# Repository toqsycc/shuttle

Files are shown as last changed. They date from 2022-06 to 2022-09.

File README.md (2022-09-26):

# Колёсный робот на базе Arduino
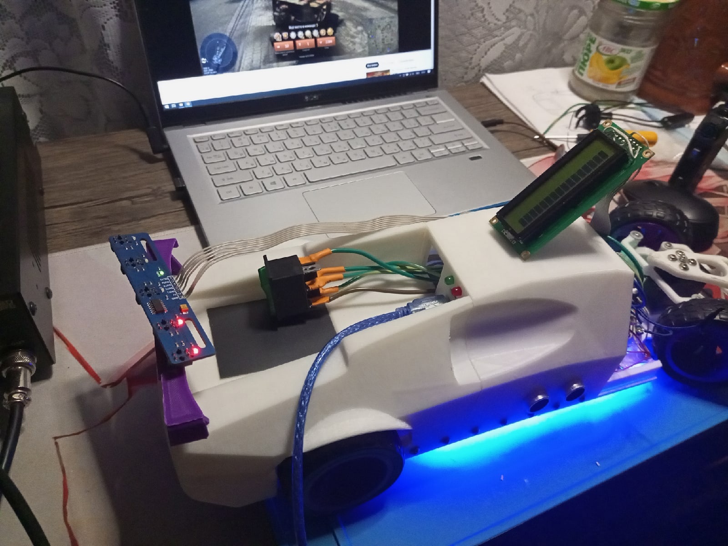
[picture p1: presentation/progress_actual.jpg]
Общий вид сборки

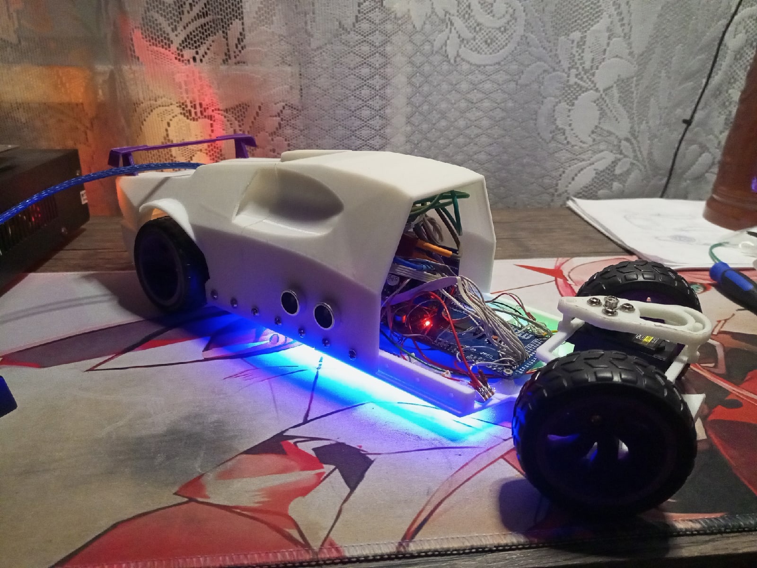
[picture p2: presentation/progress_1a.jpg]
Прогресс сборки, 1

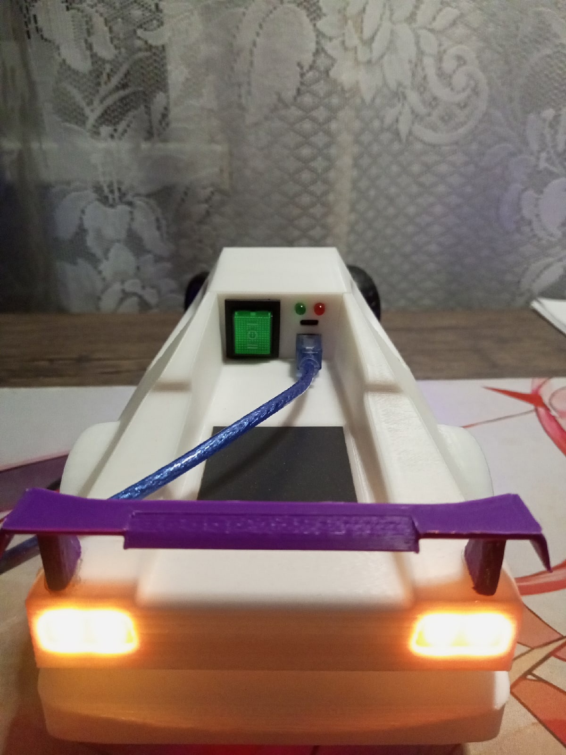
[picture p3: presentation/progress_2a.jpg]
Прогресс сборки, 2

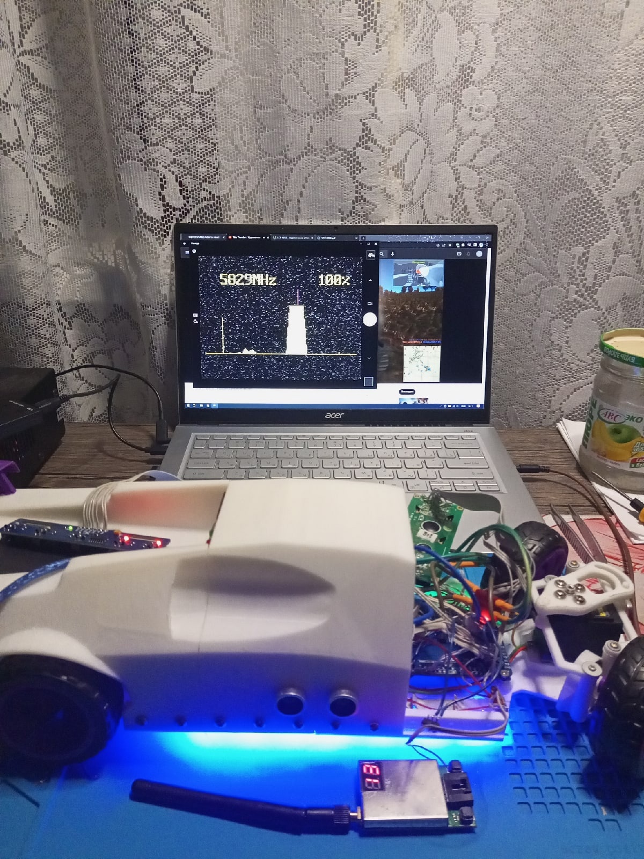
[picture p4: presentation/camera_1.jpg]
Трансляция изображения, 1

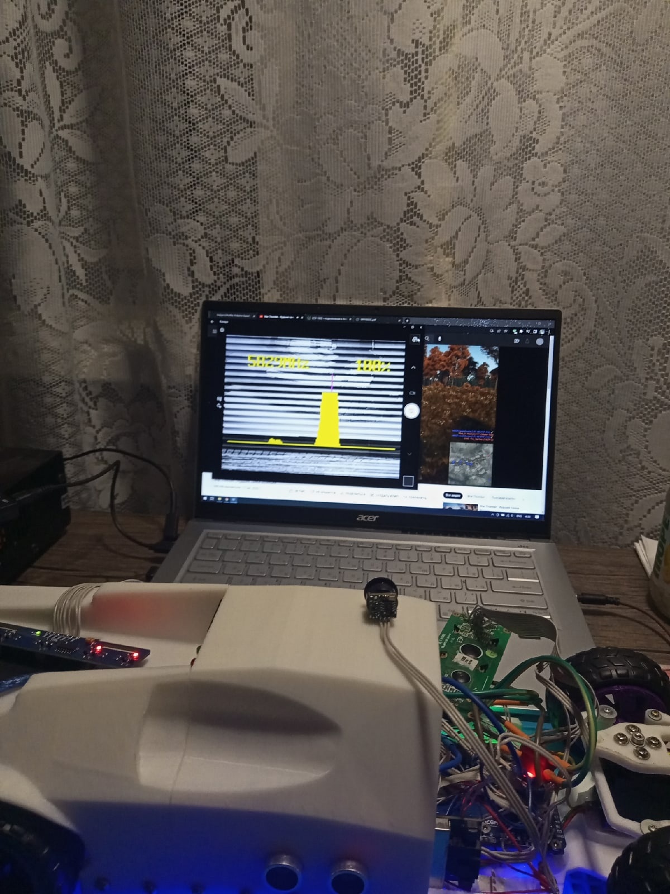
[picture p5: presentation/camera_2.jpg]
Трансляция изображения, 2


## История версий
- [x] **v0.11a**  
Внесённые изменения:
* Припаяна вся периферия;
* Добавлен передатчик видеосвязи;
* Перепрограммирован модуль радиосвязи.
- [ ] v0.1a  
Внесённые изменения:
* Завершена распайка заднего блока машины;
* Установлен задний блок корпуса, производится распайка среднего блока машины;
* Смоделирован и собран передний колёсный привод машины;
* Установлены и распаяны SPI-RGB ленты;
* Подключен и запрограммирован сервопривод.
- [ ] v0.09  
Внесённые изменения:
* Начата разработка корпуса, сделана заднаяя его часть, наполовину завершена разработка средней части корпуса;
* Обновлён скриншот.
- [ ] v0.08  
Внесённые изменения:
* Завершена разработка рамы, сделан задний бампер, впереди много интересного;
* Начата сборка, собрана рама, установлены лонжероны, некоторые электрические и электронные компоненты.
- [ ] v0.07  
Внесённые изменения:
* Изменена концепция - отказ от полного привода в пользу усиленного заднего;
* Изменена конструкция задней части рамы, исправлены диаметры некоторых отверстий, в частности, под лонжероны и стойки драйвера;
* Добавлены дугообразные вырезы глубиной 3.5 мм в задней части рамы для предотвращения зацепа рамы диском;
* Убраны недоступные отверстия по бортам задней части рамы;
* Передняя часть рамы адаптирована под подшипник ISO F625ZZ (ГОСТ 10058-90 4А-3860093);
* На задней части рамы теперь по два мотора на колесо, связанных зубчатой передачей 1:1;
* Обновлён скриншот;
* Ведётся работа над передней частью рамы.
- [ ] v0.06  
Внесённые изменения:
* Изменена длина посадочного отверстия под релейный модуль;
* Увеличено расстояние между отверстиями под диодную ленту;
* Изменено положение посадочного отверстия под релейный модуль.
- [ ] v0.05  
Внесённые изменения:
* Исправлена ширина релейного модуля и модуля драйвера;
* Увеличены отверстия под светодиодную ленту;
* Исправлено крепление батарейного отсека;
* Исправлена глубина посадки термореле и датчика температуры;
* Сделал шахту провода под батарейным блоком глубже;
* Нарастил крепления под ушки моторов.
- [ ] v0.04  
Внесённые изменения:
* Угол развала колёс уменьшен до -2.25 градусов;
* Клиренс увеличен на 2 мм;
* Увеличены диаметры отверстий под валы моторов и ключей на задней части рамы;
* Исправлены углы отклонения для RGB-ленты, подсвечивающей лонжероны;
* Исправлены отверстия под крепления лонжеронов;
* Увеличена дистанция между светодиодами ленты;
* Увеличена высота держателя моторов на 2 мм;
* Изменено положение батарейного блока и драйвера двигателей;
* Добавлены посадочные позиции для термореле и температурного датчика, а также шахты для их проводов.
- [ ] v0.03  
Внесённые изменения:
* Уменьшен размер задней рамы в соответствии с обновлёнными пропорциями.
- [ ] v 0.02  
Внесённые изменения:
* Добавлены отверстия под RGB-ленты и крепления под драйвер двигателей и реле.
- [ ] v 0.01 - **Начало работы**  
Внесённые изменения:
* Сформирована модель задней рамы в соответствии с пропорциями.
## Общая информация
Разработка в процессе
## Назначение
Робот является демонстрационной моделью для автономной езды по полигону в двух базовых режимах: *вдоль чёрной линии* или *между двух препятствий*.  
Референсом внешнего вида является суперкар Lamborghini Diablo 1991.  
Помимо автономного режима предумотрено управление через Bluetooth. С помощью встроенного ЖК-дисплея формата 1602 происходит вывод информации **на русском языке**.  
Прошивка написана на языке программирования C++ с использованием ООП.
## Аппаратные компоненты
- Arduino Mega 2560 R3
- DBH-12V Dual DC Motor Drive
- 4x TT Motors
- 5x TCRT5000 IR Line Sensor
- 2x HC-SR04 US Distance Meter
- PCA9685 PWM Servo Controller
- MG996 Servo
- AHT10 Temperature Sensor
- MPU6050 Accelerometer
- WINSTAR WH1602 LCD
- HC-05 Bluetooth Module
- HW-504 Joystick
- Relay Module 5V 10A
- TXS0108 Logic Converter
- SX1308 DC-DC Converter
## Особенности
Разработка в процессе

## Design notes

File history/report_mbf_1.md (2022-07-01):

# Крупный багфикс #1
###### Внесённые изменения:
- Добавлен вырез под фиксаторы мотора, позволяющий полностью прижать мотор к креплению;
- Угол развала изменён с -5 градусов на -2.25 градуса;
- Клиренс изменён с 18 мм на 20 мм;
- Увеличены диаметры отверстий для вала и ключа на задней раме;
- Исправил углы отклонения для RGB-ленты подсветки лонжеронов;
- Исправил дистанцию между отверстиями под светодиоды ленты;
- Исправил отверсия под крепление лонжеронов;
- Высота держателей моторов увеличена на 2 мм;
- Изменены положения батарейного блока и драйвера двигателей.

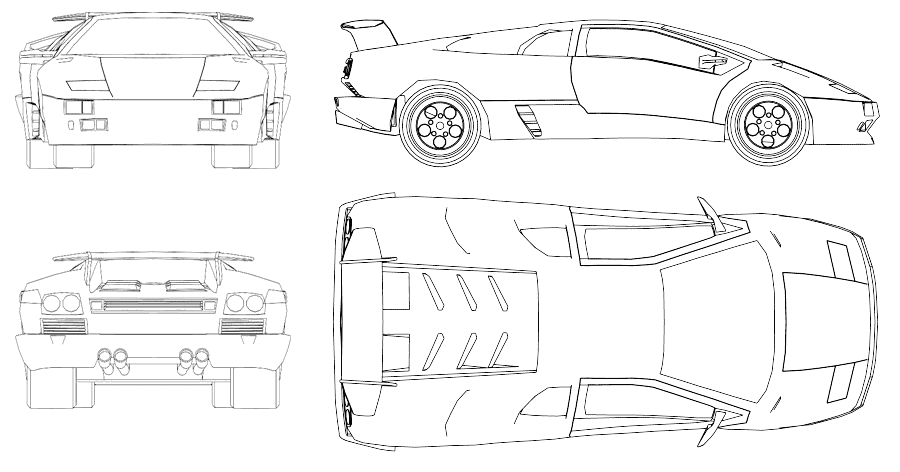
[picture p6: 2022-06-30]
presentation/reference.gif

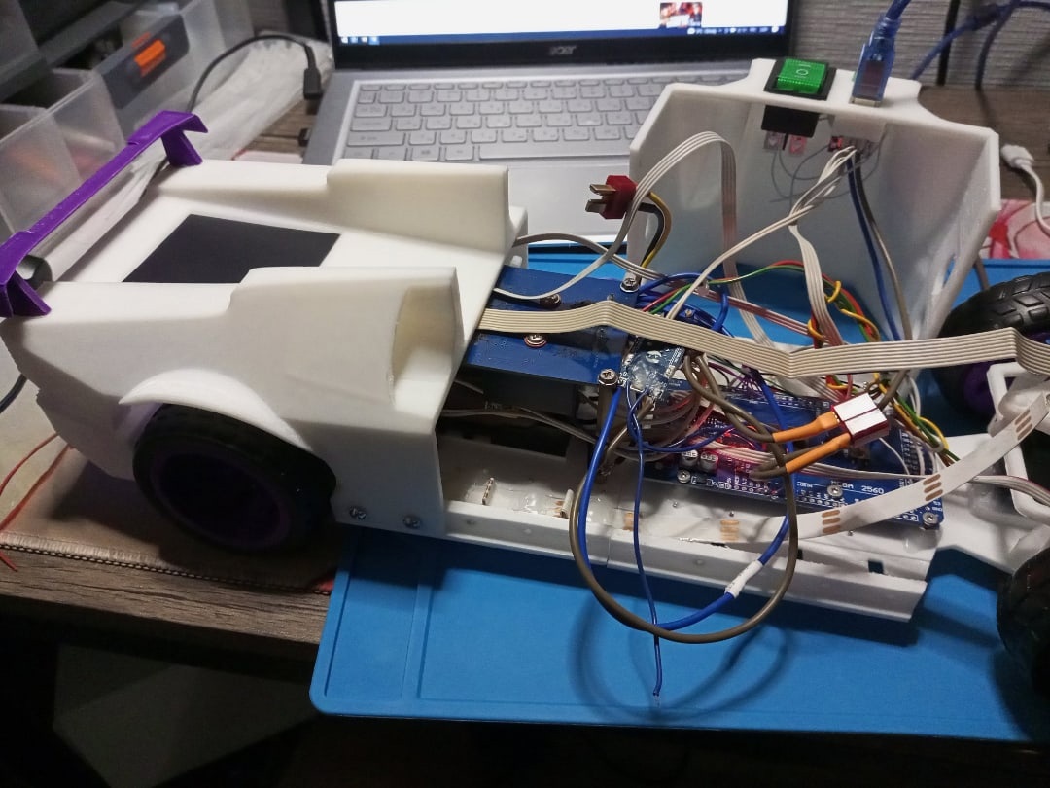
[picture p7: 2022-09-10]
presentation/progress_1.jpg

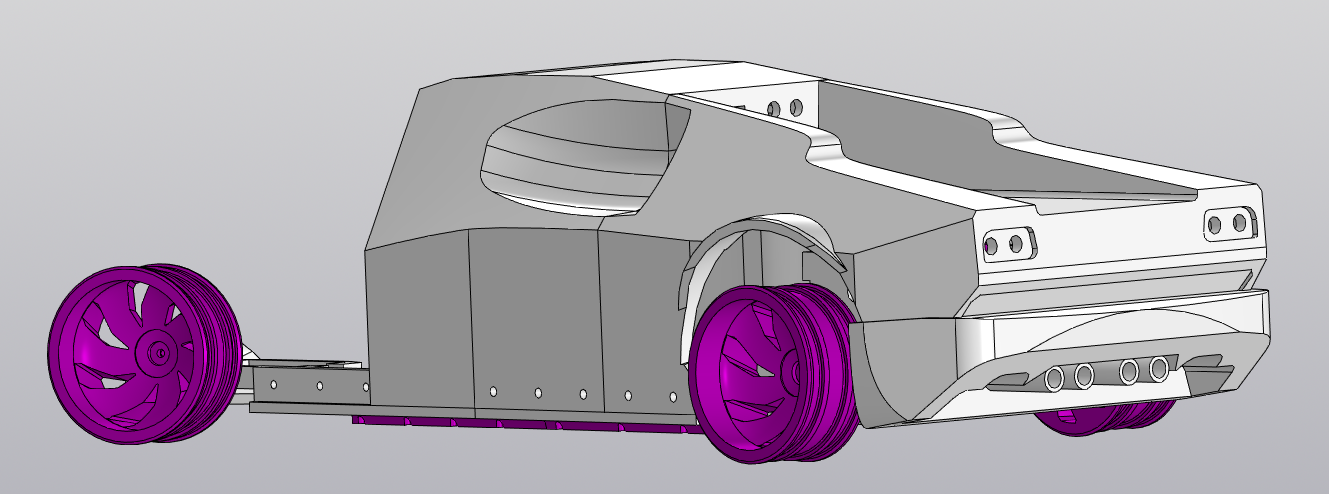
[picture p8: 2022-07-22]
presentation/screenshot.png

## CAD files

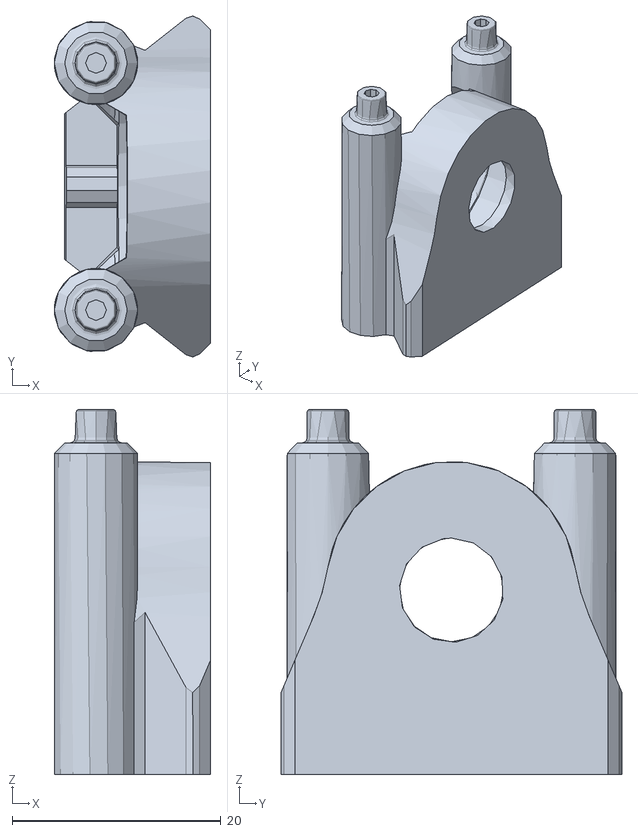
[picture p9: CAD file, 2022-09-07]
cad/print/rear_holder.stl
15.0 x 32.7 x 35.0

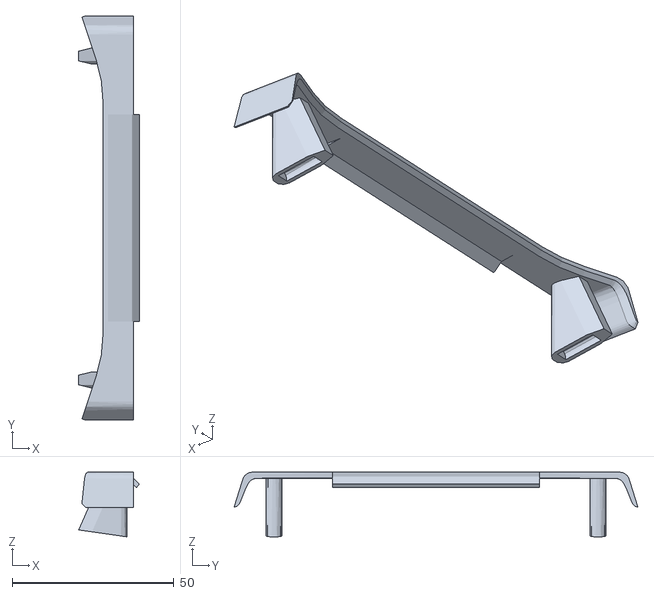
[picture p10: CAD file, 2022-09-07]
cad/print/spoiler.stl
18.7 x 124.7 x 20.0

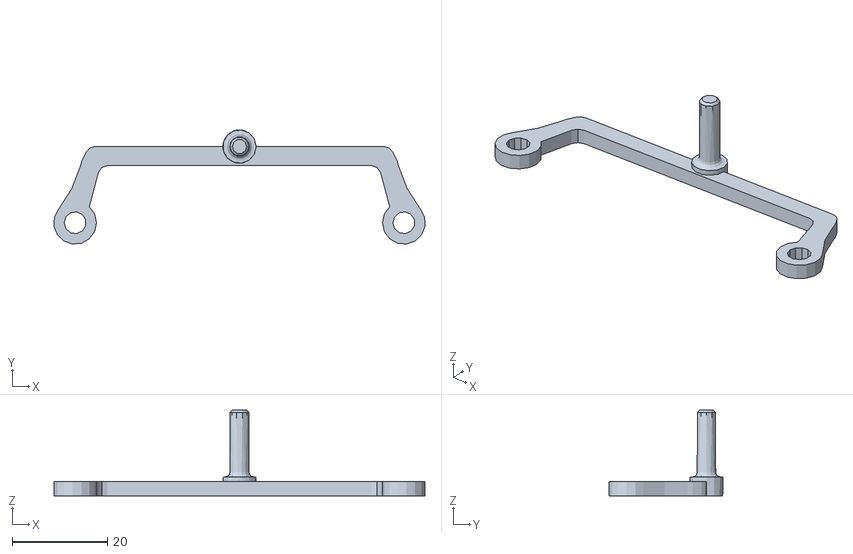
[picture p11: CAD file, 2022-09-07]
cad/print/rear_linker.stl
77.9 x 23.9 x 18.0

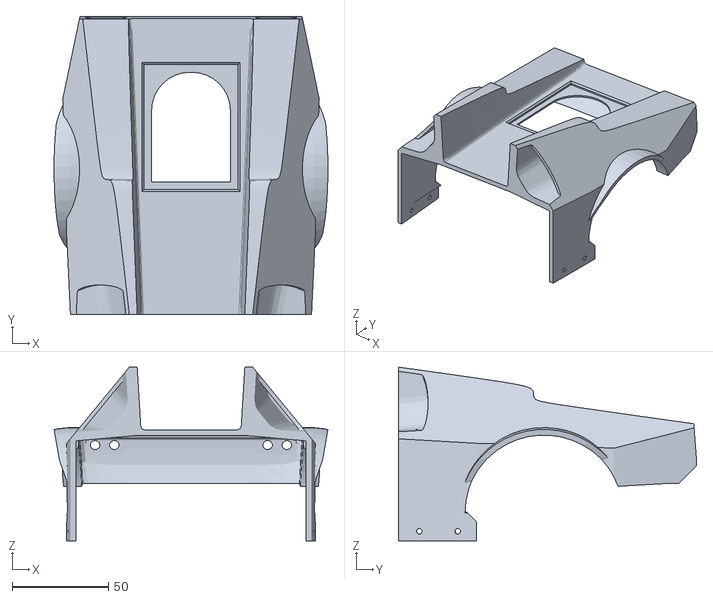
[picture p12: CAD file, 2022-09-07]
cad/print/hull-rear.stl
142.5 x 155.0 x 90.4

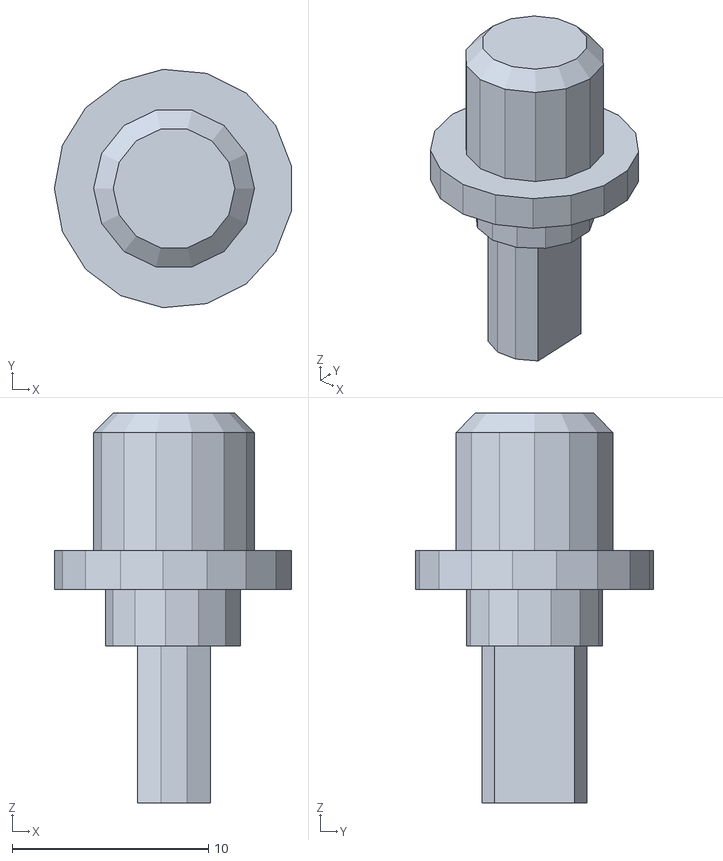
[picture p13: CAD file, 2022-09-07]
cad/print/rear_axis.stl
12.1 x 12.1 x 19.9

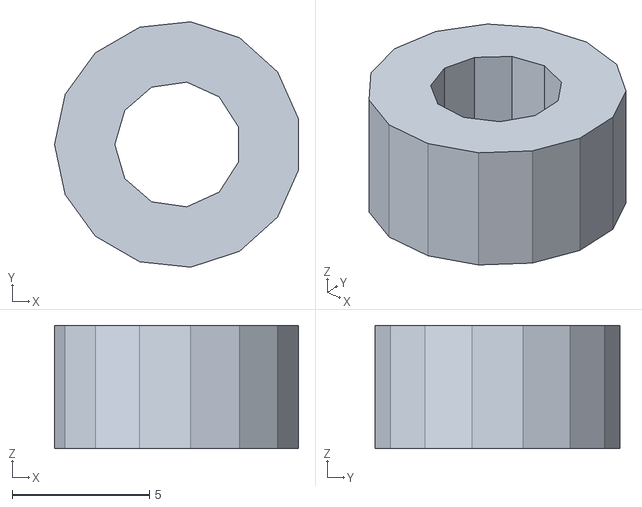
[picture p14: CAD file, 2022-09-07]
cad/print/rear_vtulka.stl
8.90 x 8.95 x 4.50

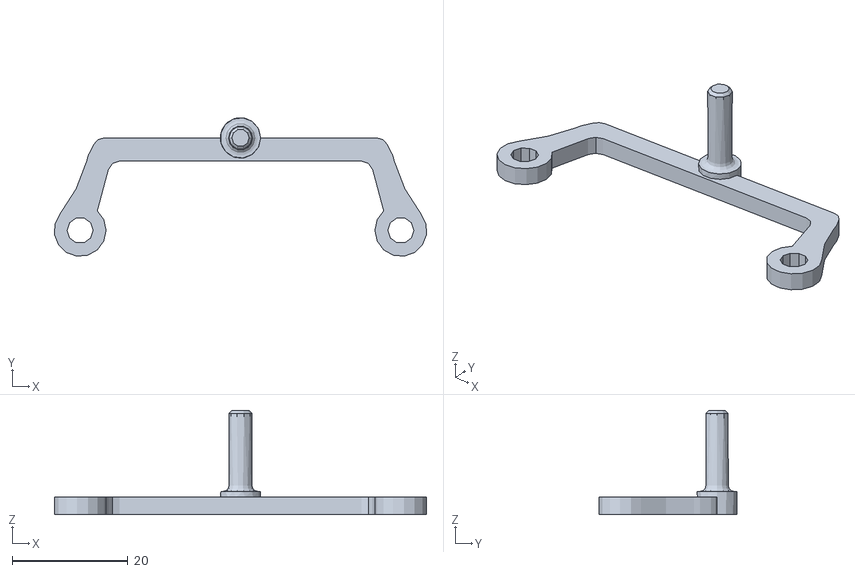
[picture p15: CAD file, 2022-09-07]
cad/print/rear_linker2.stl
64.4 x 23.9 x 18.0

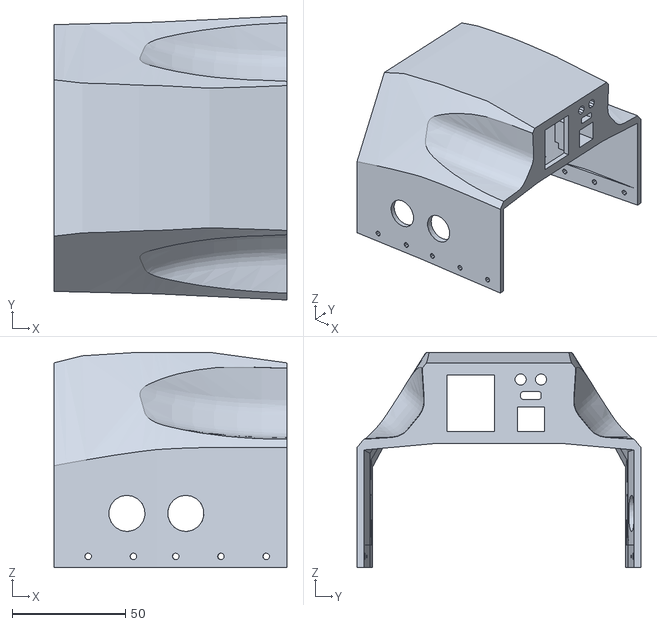
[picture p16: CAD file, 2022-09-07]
cad/print/hull-middle.stl
102.8 x 125.4 x 95.2

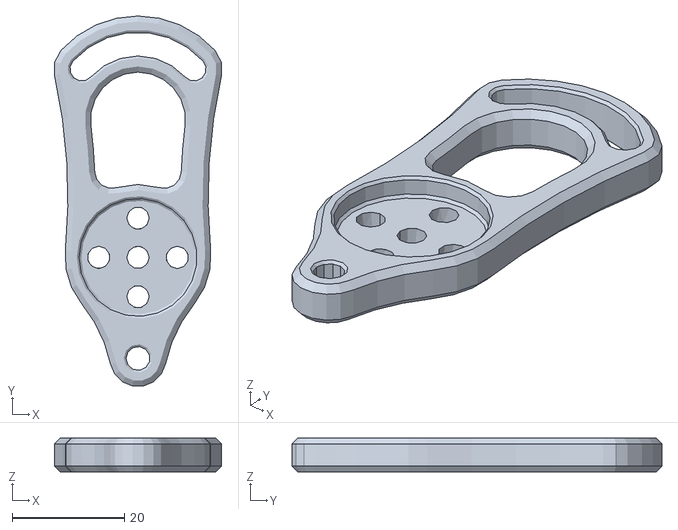
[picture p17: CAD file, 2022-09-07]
cad/print/rear_wheel.stl
29.8 x 65.9 x 6.00

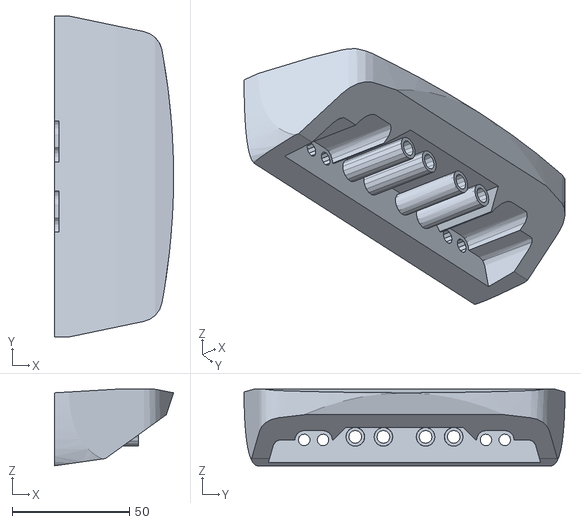
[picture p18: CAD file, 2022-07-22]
cad/print/bumper-rear.stl
50.9 x 137.0 x 32.7

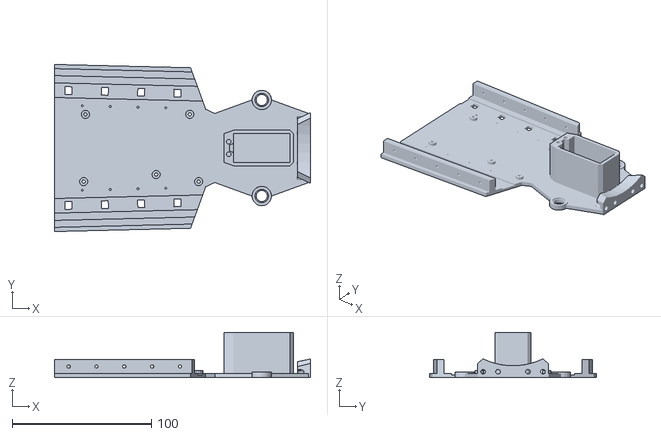
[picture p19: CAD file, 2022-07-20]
cad/print/basement-front.stl
183.8 x 120.0 x 32.5

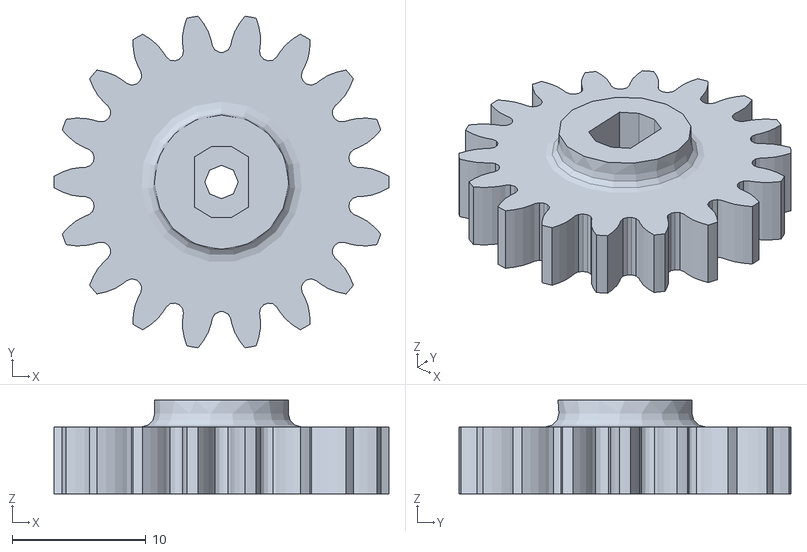
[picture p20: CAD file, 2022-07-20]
cad/print/motor_gear.stl
25.0 x 24.8 x 7.00

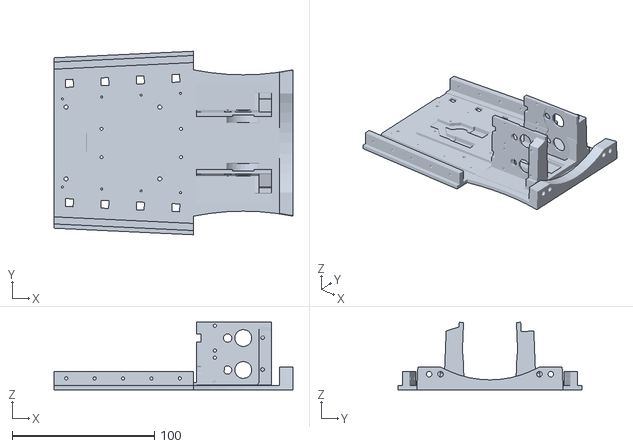
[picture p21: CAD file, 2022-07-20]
cad/print/basement-back.stl
168.3 x 129.3 x 47.6

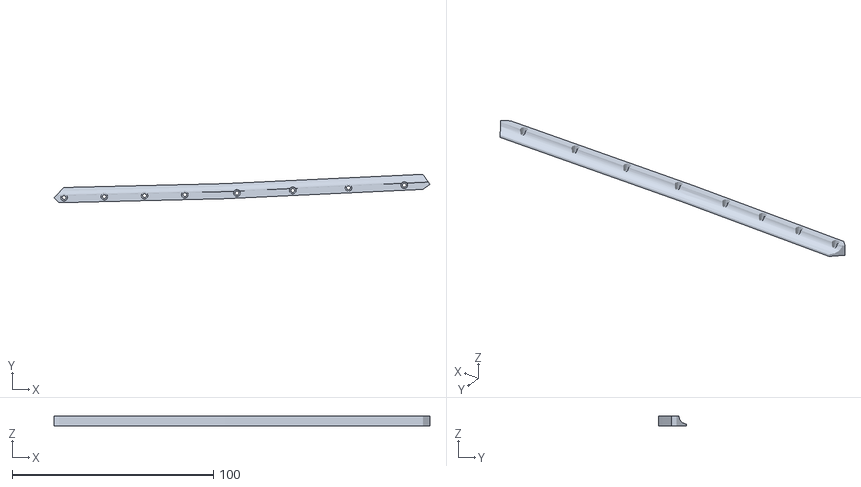
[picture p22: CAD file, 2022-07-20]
cad/print/longeron.stl
186.8 x 14.1 x 5.00

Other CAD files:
cad/print/wheel_disc.stl

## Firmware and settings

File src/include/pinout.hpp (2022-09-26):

/*
 *  Проект беспилотного устройства на базе Arduino Mega 2560
 *  Распиновка материнской платы
 * 
 *  Разработчик:    toqsycc
 *                  26.09.22
 */

// DONE: Записать пины управления двигателем, АЦП батарей и двигателей, исправить TRIG и ECHO на действительные значения
#define EXHAUST_LIGHT_B     2   // Цветные ШИМ-каналы шины выхлопа
#define EXHAUST_LIGHT_G     3   //
#define EXHAUST_LIGHT_R     4   //
#define REAR_R_LIGHT_B      8   // Цветные ШИМ-каналы шины правой задней фары
#define REAR_R_LIGHT_G      9   //
#define REAR_R_LIGHT_R      10  //
#define REAR_L_LIGHT_B      11  // Цветные ШИМ-каналы шины левой задней фары
#define REAR_L_LIGHT_G      12  //
#define REAR_L_LIGHT_R      13  //
#define SERVO_CONTROL_PIN   22  // Пин управления сервоприводом
#define RELAY_CONTROL_PIN   23  // Пин управления реле
#define STRIP_DATA_RIGHT    50  // Пин данных правой светодиодной ленты
#define STRIP_DATA_LEFT     51  // Пин данных левой светодиодной ленты
#define PS2_CLOCK_PIN       53  // Пин тактирования тачпада
#define PS2_DATA_PIN        52  // Пин данных тачпада
#define SONIC_L_TRIG        40  // Пин сигнала левого УЗ-датчика
#define SONIC_L_ECHO        42  // Пин отклика левого УЗ-датчика
#define SONIC_R_TRIG        41  // Пин сигнала правого УЗ-датчика
#define SONIC_R_ECHO        43  // Пин отклика правого УЗ-датчика
#define ENGINE_A_EN1        49  // Пин EN1-A модуля управления двигателями
#define ENGINE_A_EN2        47  // Пин EN2-A модуля управления двигателями
#define ENGINE_A_PWM        45  // Пин PWM-A модуля управления двигателями
#define ENGINE_B_EN1        48  // Пин EN1-B модуля управления двигателями
#define ENGINE_B_EN2        46  // Пин EN2-B модуля управления двигателями
#define ENGINE_B_PWM        44  // Пин PWM-B модуля управления двигателями
#define BATTERY_ENG         A0  // Пин статуса аккумулятора нагрузки
#define BATTERY_SELF        A1  // Пин статуса аккумулятора электроники
#define ENGINE_A_FDB        A2  // Пин FDB-A модуля управления двигателями
#define ENGINE_B_FDB        A3  // Пин FDB-B модуля управления двигателями
#define DISPLAY_BKL         37  // Состояние подсветки дисплея
#define DISPLAY_RS          38  // Register Select
#define DISPLAY_EN          39  // Enable
#define DISPLAY_D0          26  // Шина данных дисплея
#define DISPLAY_D1          27  //
#define DISPLAY_D2          28  //
#define DISPLAY_D3          29  //
#define DISPLAY_D4          30  //
#define DISPLAY_D5          31  //
#define DISPLAY_D6          32  //
#define DISPLAY_D7          33  //
#define INFRARED_O1         16  // Шина данных инфракрасного датчика
#define INFRARED_O2         17  //
#define INFRARED_O3         34  //
#define INFRARED_O4         35  //
#define INFRARED_O5         36  //

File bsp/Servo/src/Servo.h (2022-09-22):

/*
  Servo.h - Interrupt driven Servo library for Arduino using 16 bit timers- Version 2
  Copyright (c) 2009 Michael Margolis.  All right reserved.

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
  You should have received a copy of the GNU Lesser General Public
  License along with this library; if not, write to the Free Software
  Foundation, Inc., 51 Franklin St, Fifth Floor, Boston, MA  02110-1301  USA
*/

/* 
  A servo is activated by creating an instance of the Servo class passing 
  the desired pin to the attach() method.
  The servos are pulsed in the background using the value most recently 
  written using the write() method.

  Note that analogWrite of PWM on pins associated with the timer are 
  disabled when the first servo is attached.
  Timers are seized as needed in groups of 12 servos - 24 servos use two 
  timers, 48 servos will use four.
  The sequence used to seize timers is defined in timers.h

  The methods are:

    Servo - Class for manipulating servo motors connected to Arduino pins.

    attach(pin )  - Attaches a servo motor to an I/O pin.
    attach(pin, min, max  ) - Attaches to a pin setting min and max values in microseconds
    default min is 544, max is 2400  
 
    write()     - Sets the servo angle in degrees.  (invalid angle that is valid as pulse in microseconds is treated as microseconds)
    writeMicroseconds() - Sets the servo pulse width in microseconds 
    read()      - Gets the last written servo pulse width as an angle between 0 and 180. 
    readMicroseconds()   - Gets the last written servo pulse width in microseconds. (was read_us() in first release)
    attached()  - Returns true if there is a servo attached. 
    detach()    - Stops an attached servos from pulsing its I/O pin. 
 */

#ifndef Servo_h
#define Servo_h

#include <inttypes.h>

/* 
 * Defines for 16 bit timers used with Servo library 
 *
 * If _useTimerX is defined then TimerX is a 16 bit timer on the current board
 * timer16_Sequence_t enumerates the sequence that the timers should be allocated
 * _Nbr_16timers indicates how many 16 bit timers are available.
 */

// Architecture specific include
#if defined(ARDUINO_ARCH_AVR)
#include "ServoTimers.h"
#elif defined(ARDUINO_ARCH_SAM)
#include "sam/ServoTimers.h"
#elif defined(ARDUINO_ARCH_SAMD)
#include "samd/ServoTimers.h"
#elif defined(ARDUINO_ARCH_STM32F4)
#include "stm32f4/ServoTimers.h"
#elif defined(ARDUINO_ARCH_NRF52)
#include "nrf52/ServoTimers.h"
#elif defined(ARDUINO_ARCH_MEGAAVR)
#include "megaavr/ServoTimers.h"
#elif defined(ARDUINO_ARCH_MBED)
#include "mbed/ServoTimers.h"
#else
#error "This library only supports boards with an AVR, SAM, SAMD, NRF52 or STM32F4 processor."
#endif

#define Servo_VERSION           2     // software version of this library

#define MIN_PULSE_WIDTH       544     // the shortest pulse sent to a servo  
#define MAX_PULSE_WIDTH      2400     // the longest pulse sent to a servo 
#define DEFAULT_PULSE_WIDTH  1500     // default pulse width when servo is attached
#define REFRESH_INTERVAL    20000     // minimum time to refresh servos in microseconds 

#define SERVOS_PER_TIMER       12     // the maximum number of servos controlled by one timer 
#define MAX_SERVOS   (_Nbr_16timers  * SERVOS_PER_TIMER)

#define INVALID_SERVO         255     // flag indicating an invalid servo index

#if !defined(ARDUINO_ARCH_STM32F4)

typedef struct  {
  uint8_t nbr        :6 ;             // a pin number from 0 to 63
  uint8_t isActive   :1 ;             // true if this channel is enabled, pin not pulsed if false 
} ServoPin_t   ;  

typedef struct {
  ServoPin_t Pin;
  volatile unsigned int ticks;
} servo_t;

class Servo
{
public:
  Servo();
  uint8_t attach(int pin);           // attach the given pin to the next free channel, sets pinMode, returns channel number or 0 if failure
  uint8_t attach(int pin, int min, int max); // as above but also sets min and max values for writes. 
  void detach();
  void write(int value);             // if value is < 200 its treated as an angle, otherwise as pulse width in microseconds 
  void writeMicroseconds(int value); // Write pulse width in microseconds 
  int read();                        // returns current pulse width as an angle between 0 and 180 degrees
  int readMicroseconds();            // returns current pulse width in microseconds for this servo (was read_us() in first release)
  bool attached();                   // return true if this servo is attached, otherwise false 
private:
   uint8_t servoIndex;               // index into the channel data for this servo
   int8_t min;                       // minimum is this value times 4 added to MIN_PULSE_WIDTH    
   int8_t max;                       // maximum is this value times 4 added to MAX_PULSE_WIDTH   
};

#endif
#endif

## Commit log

2022-06-17 board testing
2022-06-17 scad upload
    [platform-back.scad]
2022-06-17 added aht10 place on back platform
    [platform-back.scad]
2022-06-30 new concept
    [basement-back.stl, wheel_disc.stl]
2022-07-05 Перевёл README на русский
2022-07-05 Небольшие фиксы
2022-07-06 Ежедневные (нет) фиксы
2022-07-06 Обновлены файлы печати
    [basement-back.stl]
2022-07-07 Ежедневные (да за что мне это?!) фиксы
    [basement-back.stl]
2022-07-07 абобус
2022-07-18 Изменение концепции проекта
2022-07-20 Огромный апдейт
    [basement-back.stl, basement-front.stl, bumper-rear.stl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]
2022-07-20 Заменил mp4 на webm - теперь видосы должны работать
2022-07-20 Попытка ещё раз фиксануть readme
2022-07-22 Ежедневное обновление
    [bumper-rear.stl, hull-rear.stl]
2022-09-07 Обновление репозитория
    [basement-back.stl, basement-front.stl, bumper-rear.stl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]
2022-09-10 Обновил шапку репозитория
    [platform-back.scad]
2022-09-22 Проект обновлён
2022-09-22 Директория BSP наполнена всем необходимым
2022-09-26 Вынес распиновку в отдельный заголовок
2022-09-26 фикс readme
